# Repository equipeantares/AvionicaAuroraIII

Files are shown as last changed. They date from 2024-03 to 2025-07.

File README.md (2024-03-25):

                                                                                                                                                      
                                                                                                                                                      
               AAA                                                                                                      IIIIIIIIIIIIIIIIIIIIIIIIIIIIII
              A:::A                                                                                                     I::::::::II::::::::II::::::::I
             A:::::A                                                                                                    I::::::::II::::::::II::::::::I
            A:::::::A                                                                                                   II::::::IIII::::::IIII::::::II
           A:::::::::A        uuuuuu    uuuuuu rrrrr   rrrrrrrrr      ooooooooooo   rrrrr   rrrrrrrrr   aaaaaaaaaaaaa     I::::I    I::::I    I::::I  
          A:::::A:::::A       u::::u    u::::u r::::rrr:::::::::r   oo:::::::::::oo r::::rrr:::::::::r  a::::::::::::a    I::::I    I::::I    I::::I  
         A:::::A A:::::A      u::::u    u::::u r:::::::::::::::::r o:::::::::::::::or:::::::::::::::::r aaaaaaaaa:::::a   I::::I    I::::I    I::::I  
        A:::::A   A:::::A     u::::u    u::::u rr::::::rrrrr::::::ro:::::ooooo:::::orr::::::rrrrr::::::r         a::::a   I::::I    I::::I    I::::I  
       A:::::A     A:::::A    u::::u    u::::u  r:::::r     r:::::ro::::o     o::::o r:::::r     r:::::r  aaaaaaa:::::a   I::::I    I::::I    I::::I  
      A:::::AAAAAAAAA:::::A   u::::u    u::::u  r:::::r     rrrrrrro::::o     o::::o r:::::r     rrrrrrraa::::::::::::a   I::::I    I::::I    I::::I  
     A:::::::::::::::::::::A  u::::u    u::::u  r:::::r            o::::o     o::::o r:::::r           a::::aaaa::::::a   I::::I    I::::I    I::::I  
    A:::::AAAAAAAAAAAAA:::::A u:::::uuuu:::::u  r:::::r            o::::o     o::::o r:::::r          a::::a    a:::::a   I::::I    I::::I    I::::I  
   A:::::A             A:::::Au:::::::::::::::uur:::::r            o:::::ooooo:::::o r:::::r          a::::a    a:::::a II::::::IIII::::::IIII::::::II
  A:::::A               A:::::Au:::::::::::::::ur:::::r            o:::::::::::::::o r:::::r          a:::::aaaa::::::a I::::::::II::::::::II::::::::I
 A:::::A                 A:::::Auu::::::::uu:::ur:::::r             oo:::::::::::oo  r:::::r           a::::::::::aa:::aI::::::::II::::::::II::::::::I
AAAAAAA                   AAAAAAA uuuuuuuu  uuuurrrrrrr               ooooooooooo    rrrrrrr            aaaaaaaaaa  aaaaIIIIIIIIIIIIIIIIIIIIIIIIIIIIII

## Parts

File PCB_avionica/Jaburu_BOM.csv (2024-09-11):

Reference | Value | Datasheet | Footprint | Qty | DNP
A1 | SD_Card_Module |  | SDcard_module:SD_Card_Module | 1
A2 | BMP280_Module |  | BMP280:BMP280_Module | 1
BT1 | Battery_Cell | ~ | Connector_Phoenix_MSTB:PhoenixContact_MSTBA_2,5_2-G_1x02_P5.00mm_Horizontal | 1
BZ1 | Buzzer | ~ | Buzzer_Beeper:Buzzer_12x9.5RM7.6 | 1
C1,C3 | 10uF | ~ | Capacitor_THT:CP_Radial_D5.0mm_P2.00mm | 2
C2,C4 | 0.1uF | ~ | Capacitor_THT:CP_Radial_D5.0mm_P2.00mm | 2
C5 | 100n | ~ | Capacitor_THT:CP_Radial_D5.0mm_P2.00mm | 1
D1 | D | ~ | Diode_THT:D_DO-34_SOD68_P7.62mm_Horizontal | 1
D2 | Red | ~ | LED_THT:LED_D3.0mm | 1
D3 | Yellow | ~ | LED_THT:LED_D3.0mm | 1
D4 | Green | ~ | LED_THT:LED_D3.0mm | 1
D5 | LED | ~ | LED_THT:LED_D5.0mm | 1
J1,J2 | Screw_Terminal_01x02 | ~ | Connector_Phoenix_MSTB:PhoenixContact_MSTBA_2,5_2-G_1x02_P5.00mm_Horizontal | 2
J3 | RESET | ~ | Connector_PinHeader_1.00mm:PinHeader_1x02_P1.00mm_Vertical | 1
J4 | Conn_01x08_Pin | ~ | MPU6050:MPU6050 | 1
J5 | VDD | ~ | Connector_PinHeader_1.00mm:PinHeader_1x02_P1.00mm_Vertical | 1
Q1,Q2 | NMOS_Substrate | https://ngspice.sourceforge.io/docs/ngspice-html-manual/manual.xhtml#cha_MOSFETs | Package_TO_SOT_THT:TO-220-3_Vertical | 2
R1 | 100 | ~ | Resistor_THT:R_Axial_DIN0207_L6.3mm_D2.5mm_P10.16mm_Horizontal | 1
R2,R5 | 220 | ~ | Resistor_THT:R_Axial_DIN0207_L6.3mm_D2.5mm_P10.16mm_Horizontal | 2
R3,R4 | 125 | ~ | Resistor_THT:R_Axial_DIN0207_L6.3mm_D2.5mm_P10.16mm_Horizontal | 2
R6 | 1M | ~ | Resistor_THT:R_Axial_DIN0207_L6.3mm_D2.5mm_P10.16mm_Horizontal | 1
U1 | AMS1117-3.3 | http://www.advanced-monolithic.com/pdf/ds1117.pdf | Package_TO_SOT_SMD:SOT-223-3_TabPin2 | 1
U2 | ESP32-DEVKIT-V1 |  | ESP32-DEVKIT-V1:MODULE_ESP32_DEVKIT_V1 | 1

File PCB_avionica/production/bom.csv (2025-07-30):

Designator | Footprint | Quantity | Value | LCSC Part #
A1 | SD_Card_Module | 1 | SD_Card_Module
A2 | BMP280_Module | 1 | BMP280_Module
BT1 | PhoenixContact_MSTBA_2,5_2-G_1x02_P5.00mm_Horizontal | 1 | Battery_Cell
BZ1 | Buzzer_12x9.5RM7.6 | 1 | Buzzer
C1, C3 | CP_Radial_D5.0mm_P2.00mm | 2 | 10uF
C2, C4 | CP_Radial_D5.0mm_P2.00mm | 2 | 0.1uF
C5 | CP_Radial_D5.0mm_P2.00mm | 1 | 100n
D1 | D_DO-34_SOD68_P7.62mm_Horizontal | 1 | D
D2 | LED_D3.0mm | 1 | Red
D3 | LED_D3.0mm | 1 | Yellow
D4 | LED_D3.0mm | 1 | Green
D5 | LED_D5.0mm | 1 | LED
H1, H2, H3, H4 | MountingHole_3.2mm_M3 | 4 | MountingHole
J1, J2 | PhoenixContact_MSTBA_2,5_2-G_1x02_P5.00mm_Horizontal | 2 | Screw_Terminal_01x02
J3 | PinSocket_2x01_P2.54mm_Vertical | 1 | RESET
J4 | MPU6050 | 1 | Conn_01x08_Pin
JP1 | SolderJumper-2_P1.3mm_Open_Pad1.0x1.5mm | 1 | LDO 3V3
JP2, JP4, JP6, JP8 | SolderJumper-2_P1.3mm_Open_Pad1.0x1.5mm | 4 | BATTERY
JP3, JP5, JP7 | SolderJumper-2_P1.3mm_Open_Pad1.0x1.5mm | 3 | ESP 3V3
Q1, Q2 | TO-220-3_Vertical | 2 | NMOS_Substrate
R1 | R_Axial_DIN0207_L6.3mm_D2.5mm_P10.16mm_Horizontal | 1 | 100
R2, R5 | R_Axial_DIN0207_L6.3mm_D2.5mm_P10.16mm_Horizontal | 2 | 220
R3, R4 | R_Axial_DIN0207_L6.3mm_D2.5mm_P10.16mm_Horizontal | 2 | 125
R6 | R_Axial_DIN0207_L6.3mm_D2.5mm_P10.16mm_Horizontal | 1 | 1M
U1 | SOT-223-3_TabPin2 | 1 | AMS1117-3.3
U2 | MODULE_ESP32_DEVKIT_V1 | 1 | ESP32-DEVKIT-V1

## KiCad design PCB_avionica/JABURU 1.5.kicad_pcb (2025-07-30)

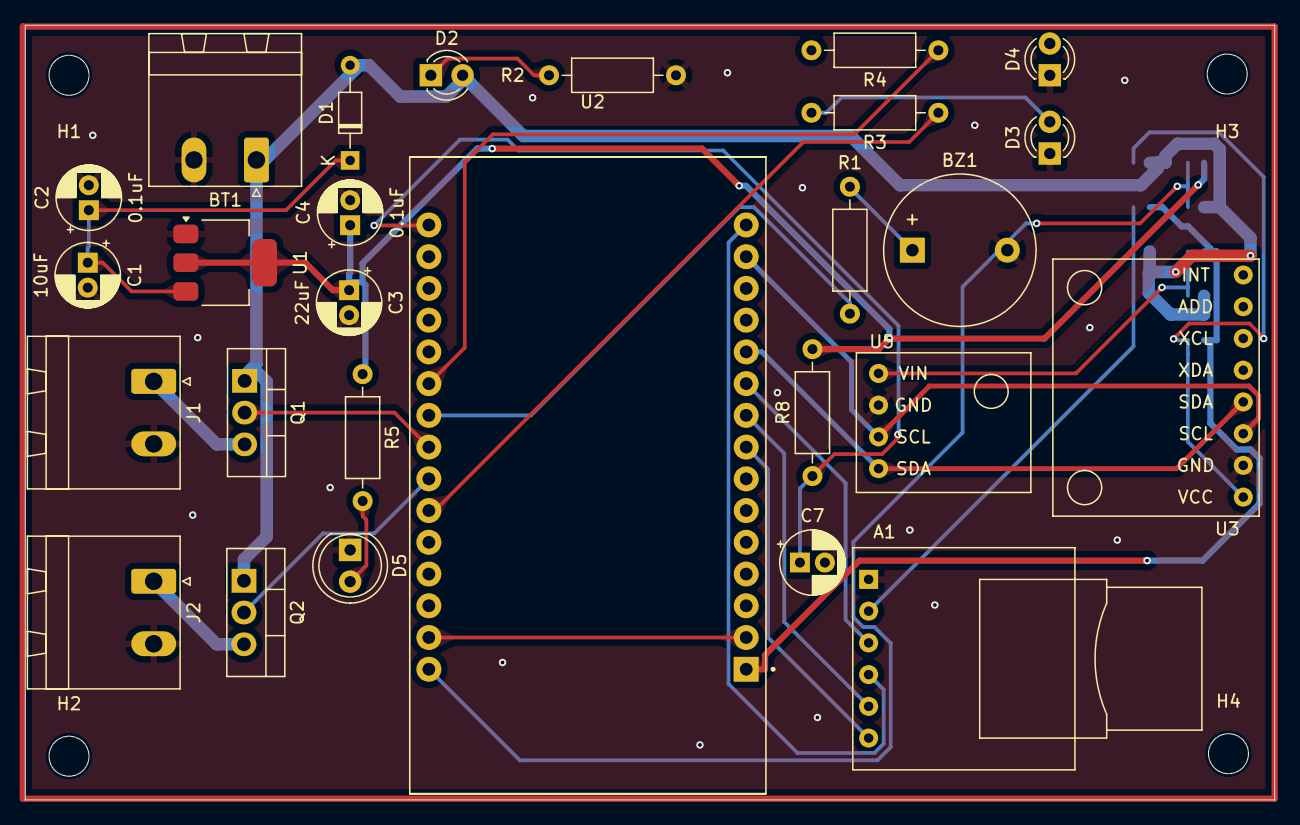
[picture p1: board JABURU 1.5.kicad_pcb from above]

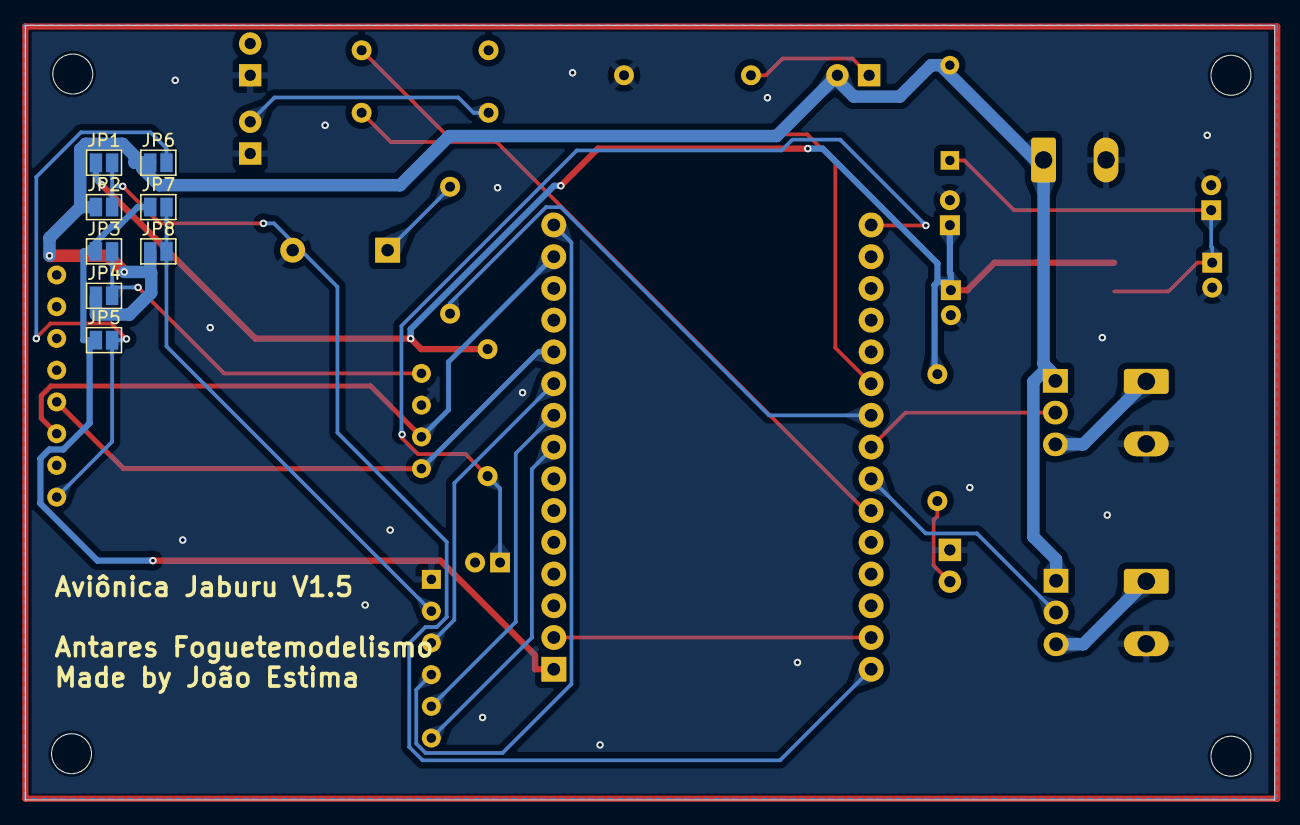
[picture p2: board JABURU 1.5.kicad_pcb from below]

Board: 2 copper layers, 100.0 x 62.0 mm, 39 parts (8 on the bottom side), 29 nets.

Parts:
A1: SD_Card_Module
BT1: Battery_Cell; PhoenixContact_MSTBA_2,5_2-G_1x02_P5.00mm_Horizontal
BZ1: Buzzer; Buzzer_12x9.5RM7.6
C1: 10uF; CP_Radial_D5.0mm_P2.00mm
C2, C4, C7: 0.1uF; CP_Radial_D5.0mm_P2.00mm
C3: 22uF; CP_Radial_D5.0mm_P2.00mm
D1: D; D_DO-34_SOD68_P7.62mm_Horizontal
D2: Red; LED_D3.0mm
D3: Yellow; LED_D3.0mm
D4: Green; LED_D3.0mm
D5: LED; LED_D5.0mm
H1, H2, H3, H4: MountingHole; MountingHole_3.2mm_M3
J1: IGN_01; PhoenixContact_MSTBA_2,5_2-G_1x02_P5.00mm_Horizontal
J2: IGN_02; PhoenixContact_MSTBA_2,5_2-G_1x02_P5.00mm_Horizontal
JP1: LDO 3V3; SolderJumper-2_P1.3mm_Open_Pad1.0x1.5mm
JP2, JP4, JP6, JP8: BATTERY; SolderJumper-2_P1.3mm_Open_Pad1.0x1.5mm
JP3, JP5, JP7: ESP 3V3; SolderJumper-2_P1.3mm_Open_Pad1.0x1.5mm
Q1, Q2: NMOS_Substrate; TO-220-3_Vertical
R1: 100; R_Axial_DIN0207_L6.3mm_D2.5mm_P10.16mm_Horizontal
R2, R5: 220; R_Axial_DIN0207_L6.3mm_D2.5mm_P10.16mm_Horizontal
R3, R4: 125; R_Axial_DIN0207_L6.3mm_D2.5mm_P10.16mm_Horizontal
R8: 10K; R_Axial_DIN0207_L6.3mm_D2.5mm_P10.16mm_Horizontal
U1: AMS1117-3.3; SOT-223-3_TabPin2
U2: ESP32-DEVKIT-V1; MODULE_ESP32_DEVKIT_V1
U3: module_mpu6050
U5: module_bme280_alt

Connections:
+3V3: C3.1, C4.1, JP1.1 (A), R5.1, R8.2, U1.2 (VO)
+BATT: BT1.1 (+), D1.2 (A), D2.2 (A), JP2.1 (A), JP4.1 (A), JP6.1 (A), JP8.1 (A), Q1.1 (D), Q2.1 (D)
BZR: R1.1, U2.22 (D33)
CSSD: A1.6 (CS), U2.8 (D5)
GND: A1.1 (GND), BT1.2 (-), BZ1.2 (+), C1.2, C2.2, C3.2, C4.2, C7.2, D3.1 (K), D4.1 (K), D5.1 (K), J1.2, J2.2, R2.1, U1.1 (GND), U3.2 (GND), U5.2 (GND)
IGN_1: Q1.2 (G), U2.23 (D25)
IGN_2: Q2.2 (G), U2.24 (D26)
LedAcionamento: R4.1, U2.21 (D32)
LedStatus: R3.1, U2.25 (D27)
MISO: A1.3 (MISO), U2.10 (D19)
MOSI: A1.4 (MOSI), U2.15 (D23)
unnamed: A1.2 (3V3), JP7.2 (B), JP8.2 (B)
unnamed: BZ1.1 (-), R1.2
unnamed: C1.1, C2.1, D1.1 (K), U1.3 (VI)
unnamed: D2.1 (K), R2.2
unnamed: D3.2 (A), R3.2
unnamed: D4.2 (A), R4.2
unnamed: D5.2 (A), R5.2
unnamed: J1.1, Q1.3 (S)
unnamed: J2.1, Q2.3 (S)
unnamed: JP1.2 (B), JP2.2 (B), U2.30 (VIN)
unnamed: JP3.2 (B), JP4.2 (B), U5.1 (VIN)
unnamed: JP5.2 (B), JP6.2 (B), U3.1 (VCC)
unnamed: C7.1, R8.1, U2.16 (EN)
unnamed: U2.2 (GND), U2.29 (GND)
SCK: A1.5 (CLK), U2.9 (D18)
SCL: U2.14 (D22), U3.3 (SCL), U5.3 (SCL)
SDA: U2.11 (D21), U3.4 (SDA), U5.4 (SDA)
VDD: JP3.1 (A), JP5.1 (A), JP7.1 (A), U2.1 (3V3)

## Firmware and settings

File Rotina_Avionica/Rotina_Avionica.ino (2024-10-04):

/*
Implementacao da rotina de execucao Avionica Aurora III

Conexoes de fiacao {
  BMP 280 {
    VCC - 3V3;
    GND - GND;
    SCL - A5;
    SDA - A4;
  }

  MPU 6050 {
    VCC - 3V3 ou 5V (se alimentacao USB);
    GND - GND;
    SCL - A5;
    SDA - A4;
  }

  Cartao microSD {
    VCC - 3V3 ou 5V;
    CS - ~10 (mas pode-se alterar para usar 4 ou 8);
    MOSI - ~11;
    CLK ou SCK - 13;
    MISO - 12;
    GND - GND;
  }
}

Pendencias {
  Sleep mode
  Implementar rotina de voo
}

Autores {
  Gabriel Rugeri;
  Henrique mago dos Bzoide;
}

Antares, 2024

Ultima modificacao: 27 09 2024, Henrique
*/

#include <Wire.h>
#include <SD.h>
#include <Adafruit_BMP280.h>
#include <SPI.h>

//Enderecos internos MPU6050 (extraidos da lib)
#define ADDR_MPU 0x68
#define MPU6050_CONFIG 0x1A      ///< General configuration register
#define MPU6050_GYRO_CONFIG 0x1B ///< Gyro specfic configuration register
#define MPU6050_ACCEL_CONFIG 0x1C ///< Accelerometer specific configration register
#define MPU6050_TEMP_H 0x41     ///< Temperature data high byte register
#define MPU6050_TEMP_L 0x42     ///< Temperature data low byte register
#define MPU6050_ACCEL_OUT 0x3B  ///< base address for sensor data reads
#define MPU6050_PWR_MGMT_1 0x6B        ///< Primary power/sleep control register
#define MPU6050_SELF_TEST_A 0x10 ///< Self test factory calibrated values register
#define ACCEL_SCALE 4096 // Fator de escala para MPU6050_RANGE_8_G
#define GYRO_SCALE 65.5 // Fator de escala para MPU6050_RANGE_500_DEG

#define SD_CS_PIN 5 // Pin onde se conecta pino CS do leitor SD

// Objeto arquivo.txt+
File dataFrame;

// Objeto BMP
Adafruit_BMP280 bmp;

//Contador de tempo
unsigned long tempoInicial;
unsigned long tempoAtual;

// Armazena dado da leitura atual
float altitude;
float altitude_anterior = 0;
float height;
float pressure;
float tempBMP;
float tempMPU;
float acceleration[3];
float gyro[3];
bool led_aceso = false;

// Auxiliares de calibracao
float calibrationHeight = 0;
float calibrationAccel[3] = {0, 0, 0};
float calibrationGyro[3] = {0, 0, 0};


void writes_on_SD(const char *grandeza, float dado, const char *unidade, char fim) {
  // Escrever no arquivo
  dataFrame.print(grandeza);
  dataFrame.print(dado); 
  dataFrame.print(" ");
  dataFrame.print(unidade);
  dataFrame.print(fim);
}


void reads_MPU() {
  
  Wire.beginTransmission(ADDR_MPU);
  Wire.write(MPU6050_CONFIG);
  Wire.write(0x05);
  Wire.endTransmission();

  // Leitura giroscopio
  Wire.beginTransmission(ADDR_MPU);
  Wire.write(MPU6050_GYRO_CONFIG);
  Wire.write(0x8);
  Wire.endTransmission();

  Wire.beginTransmission(ADDR_MPU);
  Wire.write(0x43);
  Wire.endTransmission();

  Wire.requestFrom(ADDR_MPU, 6, true);
  
  gyro[0] = Wire.read() << 8 | Wire.read();  //0x43 (GYRO_XOUT_H) & 0x44 (GYRO_XOUT_L)     
  gyro[1] = Wire.read() << 8 | Wire.read();  //0x45 (GYRO_YOUT_H) & 0x46 (GYRO_YOUT_L)
  gyro[2] = Wire.read() << 8 | Wire.read();  //0x47 (GYRO_ZOUT_H) & 0x48 (GYRO_ZOUT_L)

  gyro[0] /= GYRO_SCALE;
  gyro[1] /= GYRO_SCALE;
  gyro[2] /= GYRO_SCALE;

  // Leitura aceleracao e temperatura
  Wire.beginTransmission(ADDR_MPU);
  Wire.write(MPU6050_ACCEL_CONFIG);
  Wire.write(MPU6050_SELF_TEST_A);
  Wire.endTransmission();

  Wire.beginTransmission(ADDR_MPU);
  Wire.write(MPU6050_ACCEL_OUT);
  Wire.endTransmission();

  Wire.requestFrom(ADDR_MPU, 6, true);

  acceleration[0] = Wire.read() << 8 | Wire.read();  //0x3B (ACCEL_XOUT_H) & 0x3C (ACCEL_XOUT_L)  
  acceleration[1] = Wire.read() << 8 | Wire.read();  //0x3D (ACCEL_YOUT_H) & 0x3E (ACCEL_YOUT_L)  
  acceleration[2] = Wire.read() << 8 | Wire.read();  //0x3F (ACCEL_ZOUT_H) & 0x40 (ACCEL_ZOUT_L) 

  acceleration[0] /= ACCEL_SCALE;
  acceleration[1] /= ACCEL_SCALE;
  acceleration[2] /= ACCEL_SCALE; 

  tempMPU = Wire.read() << 8 | Wire.read();  //0x41 (TEMP_OUT_H) & 0x42 (TEMP_OUT_L)
  tempMPU = tempMPU / 340.00 + 36.53;
}


void calibrates_MPU() {
  Serial.println("Calibrando MPU6050...");
  for (int i = 0; i < 2000; i++) {
    reads_MPU();

    calibrationAccel[0] += acceleration[0];
    calibrationAccel[1] += acceleration[1];
    calibrationAccel[2] += acceleration[2];

    calibrationGyro[0] += gyro[0];
    calibrationGyro[1] += gyro[1];
    calibrationGyro[2] += gyro[2];
  }

  calibrationAccel[0] /= 2000;
  calibrationAccel[1] /= 2000;
  calibrationAccel[2] /= 2000;

  calibrationGyro[0] /= 2000;
  calibrationGyro[1] /= 2000;
  calibrationGyro[2] /= 2000;

  Serial.println("MPU6050 calibrado.");
  writes_on_SD("Aceleracao X", calibrationAccel[0], "m/s^2", '\n');
  writes_on_SD("Aceleracao Y", calibrationAccel[1], "m/s^2", '\n');
  writes_on_SD("Aceleracao Z", calibrationAccel[2], "m/s^2", '\n');
  writes_on_SD("Gyro X", calibrationAccel[0], "rad/s", '\n');
  writes_on_SD("Gyro Y", calibrationAccel[1], "rad/s", '\n');
  writes_on_SD("Gyro Z", calibrationAccel[2], "rad/s", '\n');
}


void starts_up_MPU() {
  Serial.println("Inicializando MPU6050...");

  pinMode(21, OUTPUT);
  digitalWrite(21, HIGH);

  Wire.setClock(400000);
  Wire.begin();
  delay(250);
  
  Wire.beginTransmission(ADDR_MPU);
  Wire.write(MPU6050_PWR_MGMT_1);
  Wire.write(0x00);

  Wire.endTransmission();

  calibrates_MPU();
}


void calibrates_BMP() {
  for (int i = 0; i < 2000; i++) {
    calibrationHeight += bmp.readAltitude(1013.25);
  }
  calibrationHeight /= 2000;
  Serial.println("BMP280 calibrado.");
  writes_on_SD("Altitude", calibrationHeight, "m", '\n');
}


void starts_up_BMP() {
  if (!bmp.begin()) {
    Serial.println("Falha ao inicializar BMP280.");
    while (1)
      delay(10);
  } else
    Serial.println("Sensor BMP280 inicializado com sucesso!");

    // Configuracoes padrao do datasheet
  bmp.setSampling(Adafruit_BMP280::MODE_NORMAL,     
                  Adafruit_BMP280::SAMPLING_X2,     
                  Adafruit_BMP280::SAMPLING_X16,    
                  Adafruit_BMP280::FILTER_X16,      
                  Adafruit_BMP280::STANDBY_MS_500); 

  calibrates_BMP();
}


void starts_up_SD() {
  if (!SD.begin(SD_CS_PIN)) {
    Serial.println("Falha ao inicializar leitor microSD");
    while (1)
      delay(10);
  } else
    Serial.println("Leitor microSD inicializado com sucesso.");
}


void starts_up_serial(int baud) {
  Serial.begin(baud);
  while (!Serial)
    delay(100);
  Serial.println("Monitor Serial inicializado com sucesso.");
}


void setup() {
  pinMode(25, OUTPUT);
  
  tempoInicial = millis();

  // Inicializacao dos componentes
  starts_up_serial(9600);
  starts_up_BMP();
  starts_up_MPU();
  starts_up_SD();
}


void loop() {

  dataFrame = SD.open("dados.txt", FILE_WRITE);

  if (dataFrame) {
    Serial.println("Arquivo dataframe.txt aberto. Escrevendo em dataframe.txt...");

    // Contador de tempo
    tempoAtual = millis() - tempoInicial;
    writes_on_SD("Tempo", tempoAtual, "ms", '\t');

      /* Leitura do BMP */

    // Altitude
    altitude = bmp.readAltitude(1013.25); // Pressao padrao ao nivel de mar
    writes_on_SD("Altitude", altitude, "m", '\t');

    // Altura
    height = altitude - calibrationHeight;
    writes_on_SD("Altura", height, "m", '\t');

    // Pressao atmosferica
    pressure = bmp.readPressure();
    writes_on_SD("Pressao", pressure, "Pa", '\t');

    // Temperatura BMP
    tempBMP = bmp.readTemperature();
    writes_on_SD("Temperatura (BMP)", tempBMP, "oC", '\t');

    delay(100);

      /* Leitura do MPU: aceleracao, rotacao e temperatura */
    reads_MPU();

    // Temperatura
    writes_on_SD("Temperatura (MPU)", tempMPU, "oC", '\t');

    // Aceleracao (x)
    acceleration[0] -= calibrationAccel[0];
    writes_on_SD("Aceleracao (x)", acceleration[0], "m/s^2", '\t');

    // Aceleracao (y)
    acceleration[1] -= calibrationAccel[1];
    writes_on_SD("Aceleracao (y)", acceleration[1], "m/s^2", '\t');

    // Aceleracao (z)
    acceleration[2] -= calibrationAccel[2];
    writes_on_SD("Aceleracao (z)", acceleration[2], "m/s^2", '\t');

    // Gyro (x)
    gyro[0] -= calibrationAccel[0];
    writes_on_SD("Gyro (x)", gyro[0], "rad/s", '\t');

    // Gyro (y)
    gyro[1] -= calibrationAccel[1];
    writes_on_SD("Gyro (y)", gyro[1], "rad/s", '\t');

    // Gyro (z)
    gyro[2] -= calibrationAccel[2];
    writes_on_SD("Gyro (z)", gyro[2], "rad/s", '\n'); //Considerar usar \r\n

    // Fecha arquivo dataframe.txt
    dataFrame.close();
  } else
    Serial.println("Erro ao abrir arquivo dataframe.txt");
  
  if(!led_aceso) {
    if(altitude < altitude_anterior) {
      digitalWrite(25, HIGH);
      led_aceso = true;
    }
    else {
      altitude_anterior = altitude;
    }
  }
  
  delay(100);
}

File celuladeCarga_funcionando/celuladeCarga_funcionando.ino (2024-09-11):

#include "HX711.h"
#include <SD.h>
#include <SPI.h>
#include <stdio.h>

#define calibration_factor 870 // Fator de calibração obtido previamente em outro código
#define LOADCELL_DOUT_PIN  A1
#define LOADCELL_SCK_PIN  A0

#define SD_CS_PIN 10 // Pin onde se conecta pino CS do leitor SD

char contagem = 0;
HX711 scale;
File dataFile;

void write_on_SD(float dado) {
  if (dataFile) {
    dataFile.print(dado);
    dataFile.print(" N");
    dataFile.print("\n");
    dataFile.flush(); // Ensure the data is written to the file
  } else {
    Serial.println("Error: Could not write to SD card.");
  }
}

void setup() {
  Serial.begin(9600);
  Serial.println("HX711 scale demo");

  // Initialize HX711
  scale.begin(LOADCELL_DOUT_PIN, LOADCELL_SCK_PIN);
  scale.set_scale(calibration_factor); // This value is obtained by using the SparkFun_HX711_Calibration sketch
  scale.tare(); // Assuming there is no weight on the scale at start up, reset the scale to 0
  Serial.begin(9600);
  Serial.println("HX711 scale demo");

  // Initialize HX711
  scale.begin(LOADCELL_DOUT_PIN, LOADCELL_SCK_PIN);
  scale.set_scale(calibration_factor); // This value is obtained by using the SparkFun_HX711_Calibration sketch
  scale.tare(); // Assuming there is no weight on the scale at start up, reset the scale to 0

  // Initialize SD card
  if (!SD.begin(SD_CS_PIN)) {
    //Serial.println("Error initializing SD card.");
    return;
  } else {
    Serial.println("SD card initialized successfully.");
  }

  // Open or create the file on the SD card
  dataFile = SD.open("data.txt", FILE_WRITE);
  if (!dataFile) {
    Serial.println("Error opening data.txt on SD card.");
    return;
  } else {
    Serial.println("data.txt opened successfully.");
  }

  Serial.println("Readings:");
}

void taragem() {
  if (Serial.available()) {
    char cara = Serial.read();
    if (cara == 't') {
      scale.tare();
      Serial.println("Scale tared.");
    }
  }
}

void loop() {
  float dado = scale.get_units();
  Serial.print("Reading: ");
  Serial.print(dado, 3); // scale.get_units() returns a float
  Serial.print(" N"); // You can change this to kg but you'll need to refactor the calibration_factor
  Serial.println();
  
  write_on_SD(dado);
  taragem();
}

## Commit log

2024-03-24 Codigos do MPU usando somente a biblioteca I2C e o codigo junto com o MPU
2024-03-25 PCB-1v0_bmp280+mpu6050+microsd+dual deploy
2024-04-04 Abre/fecha arquivo, identificacao de pinos
2024-05-23 Exclusao de comandos print
2024-09-05 Ajustei o código da avionica para última
2024-09-11 Coloquei o código da célula de carga + MicroSD junto com a aviônica
2024-09-11 PCB's da aviônica e código da célula de carga
    [AvionicaArapacu.kicad_pcb, AvionicaArapacu.kicad_sch, AvionicaJaburu.kicad_pcb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]
2024-09-11 Voltei a verão da rotina para última commitada pelo Rugire
2024-09-24 Aviônica Jaburu pino buzzer atualizado
    [AvionicaJaburu.kicad_pcb, AvionicaJaburu.kicad_sch, bom.csv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]
2024-09-27 Update Rotina_Avionica.ino
    implementada para o esp32
2024-10-14 Aviônica com furações e MOSFET atualizados
    [AvionicaJaburu.kicad_pcb, AvionicaJaburu.kicad_sch, bom.csv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]
2024-10-17 Mudanças no footprint do esp32 na aviônica - retirei os mounting holes do footprint do esp32
    [AvionicaJaburu.kicad_pcb]
2024-10-21 Adicionado bypass na alimentaçção dos módulos da avionica Jaburu
    [AvionicaJaburu.kicad_pcb, bom.csv, designators.csv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]
2024-11-07 outline da Jaburu corrigido pra fabricação
    [AvionicaJaburu.kicad_pcb, AvionicaJaburu.kicad_sch]
2024-11-13 correção na diferença entre o clearence e o furo metálico que deve ser >= 0.2mm
    [AvionicaJaburu.kicad_pcb]
2024-11-21 tirei qualquer pinheader com diametro menor que 2.54mm pq a fabricante não aceita
    [AvionicaJaburu.kicad_pcb, bom.csv, designators.csv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]
